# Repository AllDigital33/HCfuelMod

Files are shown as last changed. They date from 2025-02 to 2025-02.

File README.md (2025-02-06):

# HalfCat Mojave Sphinx Fuel Bulkhead Mod

OVERVIEW AND BACKGROUND

The HC Mojave Sphinx works great exactly as designed in HCR-5100. It is battle tested with over 50 firings and flights. 

After building, firing, and flying our Sinnoh Sphinx+ we noticed a small amount of IPA leaking from our fuel bulkhead when we went horizontal after filling and we noticed some small fuel leaks while pressurizing on the pad from camera footage post-flight. These leaks were minor and did not prevent the rocket from properly pressurizing, firing, or launching. The stock 4” aluminum tank tube and the +/- .013” ID tolerance is a wide variable, so we wanted to design a one-piece bulkhead with two o-rings to minimize the risk of a leak. 

We also were not fond of the two recovery bulkhead posts and their gasket washers, so we redesigned the aft recovery anchor plate to not use the bolts. That freed up room in the fuel bulkhead, so we added a 1/8” NPT tube and small valve we could use to fill fuel after the bulkhead had been secured to the tank. This allows us to assemble the piston and fuel bulkhead at home and then “load and go” on the range. 

SPECIAL CONSIDERATIONS

This mod, as designed, will only work if you are using a standard 4” fiberglass airframe for your recovery section. That was an upgrade in our original build. The stock Mojave Sphinx uses a cardboard recovery airframe that cannot support the snap forces of the drogue with the relocated aft recovery bulkhead (anchor).   

Read the attached PDF for more details.

Mike & Preston

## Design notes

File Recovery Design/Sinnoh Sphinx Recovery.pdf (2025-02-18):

# HalfCat Mojave Sphinx Sinnoh Sphinx+ Recovery

February 2025

# Modified Fiberglass Recovery

A big part of the "plus" in our Sphinx+ is the upgraded recovery section. It is a similar dual-deploy layout, but we used standard rocketry 4" fiberglass airframe and coupler, along with a commercial fiberglass nosecone (26" 5:1 Ogive). Our avionics bay is extended (13"), because we run our own flight computer ("Rocket Talk") and use a 12" 433 Mhz dipole antenna. Our avBay, nose, and aft bulkheads are all 1/8" aluminum with stainless steel u-bolt anchors. We use a nine foot Rocketman parachute and a three foot drogue with 1/2 kevlar shock cord from OneBadHawk. This gives us a soft landing in the 25fps range. Overall, our longer and heavier recovery section adds about five pounds to the build, but it is substantially stronger and will last longer (or survive harder landings).

The ID of 4" rocket fiberglass (e.g. Wildman Rocketry) is smaller than the cardboard ID specified in the Mojave Sphinx build, so you need to decrease the size of the INRG 200S airframe coupler to 3.9". The same is true for the Bulkhead Fuel Rec, AvBay bulkheads, and you will need a different bulkhead for the nose. In the nosecone we put our bulkhead about 6" from the tip and use the inside of the nose for the main chute.

Mike & Preston

@RocketTalk33 on the HC Discord

# Recovery Comparison

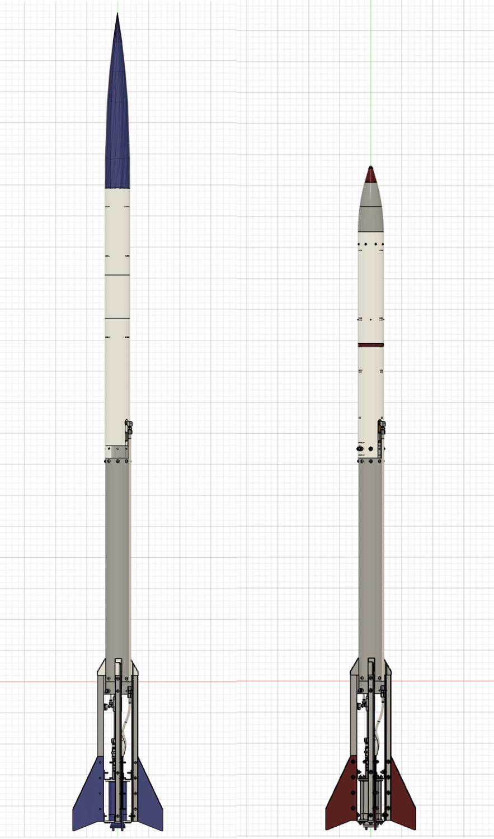
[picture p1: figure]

Sinnoh Sphinx+
(Fiberglass Recovery)

Mojave Sphinx

# Recovery Specs

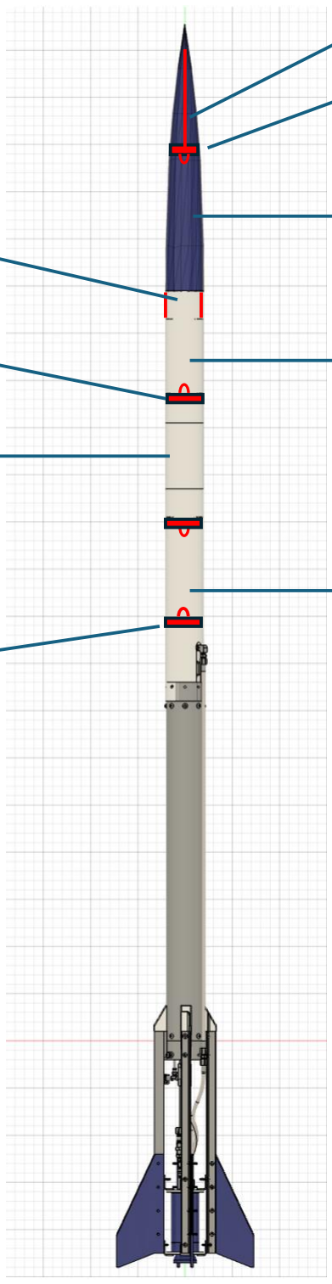
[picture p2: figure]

Sinnoh Sphinx+
(Fiberglass Recovery)

Lower (drogue) airframe
22.5” x 4” fiberglass
(can likely be a few inches shorter)

Upper (main) airframe
14” x 4” fiberglass

24” nosecone (5:1 ogive)
w/standard coupler

Internal bulkhead w/U-bolt (custom machined – see step)

Threaded Rod

Extended avionics bay for additional electronics
(regular build could use a 9” avBay coupler with 1.5” switchband)

Aluminum custom avBay bulkhead with U-bolt (avBay top and bottom)

Aluminum custom ”floating” bulkhead with U-bolt (details next page)

4-40 nylon shear pins (x4)

# Floating AFT anchor plate

3” coupler epoxied into airframe and reinforced with two PEM screws

Aluminum custom ”floating” bulkhead with U-bolt

5” floating coupler provides aft retention for the bulkhead.

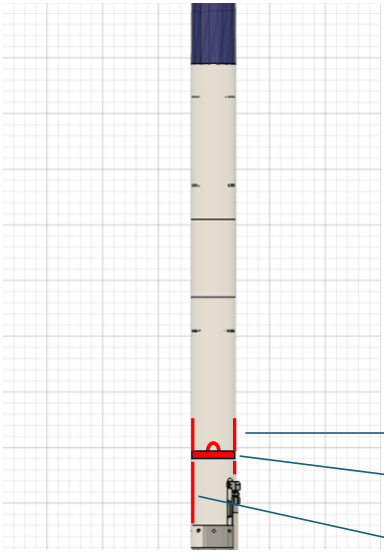
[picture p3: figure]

Note: use the same templates for airframe bolt holes and fuel plumbing cut-out. Use Dremel with carbon saw to cut fiberglass.

# Extended Avionics Bay

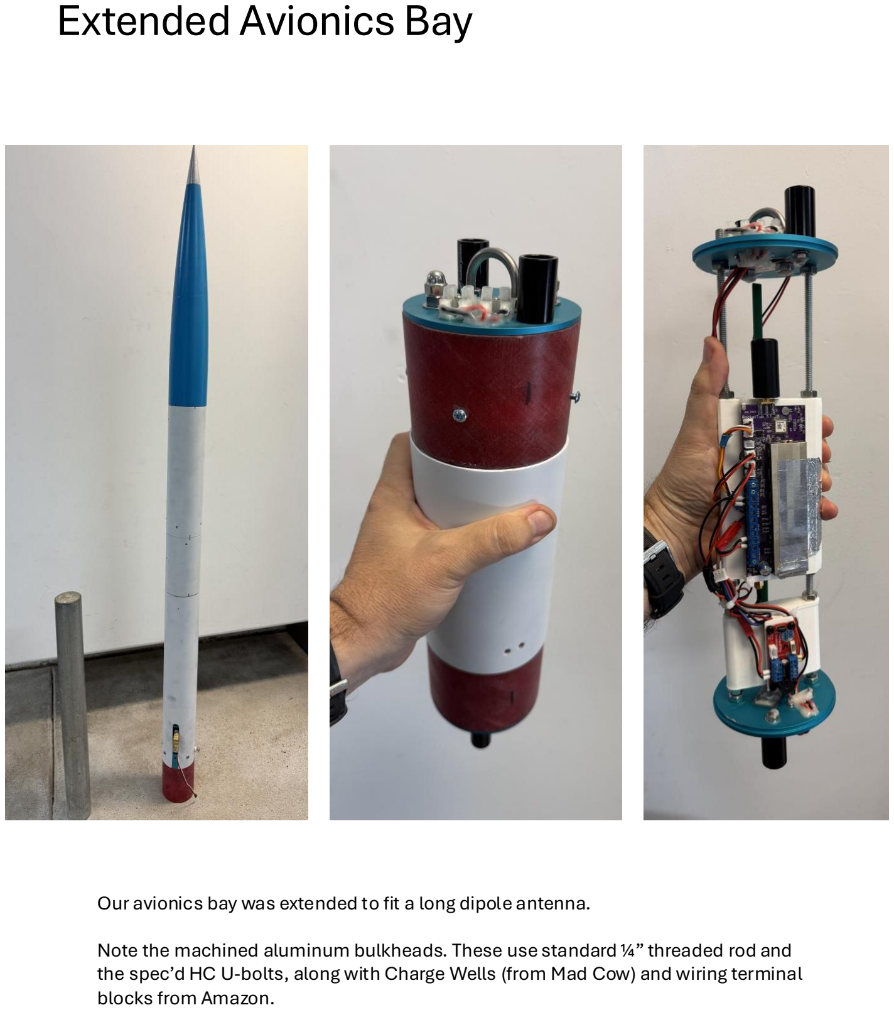
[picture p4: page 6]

Our avionics bay was extended to fit a long dipole antenna.

Note the machined aluminum bulkheads. These use standard ¼” threaded rod and the spec’d HC U-bolts, along with Charge Wells (from Mad Cow) and wiring terminal blocks from Amazon.

# BOM / Sources

Here is a list of the non-standard stuff we used for our recovery

1. 4” Fiberglass airframe (Wildman Rocketry link) (https://wildmanrocketry.com/collections/fiberglass-1/products/g12-4-0)
- Cut to 22.5” lower airframe and 14” upper airframe
2. 4” Fiberglass coupler for avBay (Wildman Rocketry link) (https://wildmanrocketry.com/collections/coupler-fiberglass/products/g12ct-4-0)
- Standard avBay would use 9”
3. 1” switchband for avBay (Wildman Rocketry link) (https://wildmanrocketry.com/collections/switch-band/products/switch-band-98mm-1-inch-wide)
4. 4” x 24” nosecone w/coupler 5:1 Ogive (Wildman Rocketry link) (https://wildmanrocketry.com/collections/nosecone/products/fnc4-0-5-1-vk-fw-mt-copy?variant=46732332695802)
5. Rocketman 9 foot standard chute (link) (https://the-rocketman.com/chutes.html/)
6. Rocketman 3 foot drogue (link) (https://the-rocketman.com/pro-x/)
7. 3/8” 30’ tubular Kevlar shock cord 3 loop (x2) (Mad Cow link) (https://www.madcowrocketry.com/3-8-x-30ft-tubular-kevlar-harness-with-3-sewn-loops/)
8. Nylon 4-40 shear pins x 4 (Chris’ rocket supplies link) (https://www.csrocketry.com/recovery-supplies/shear-pins/shear-pin-4/40.html)
9. Nosecone machined bulkhead (see STEP file)
10. avBay machined bulkhead x 2 (see STEP file)
1. Charge wells x 4 (link) (https://www.madcowrocketry.com/3-gram-aluminum-charge-wells/)
2. Terminal blocks (link) (https://a.co/d/2t4Hk0z)

For the lower airframe “floating” bulkhead see the other mod write-up here: https://github.com/AllDigital33/HCfuelMod/

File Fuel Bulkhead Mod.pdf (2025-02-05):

# HalfCat Mojave Sphinx Fuel Bulkhead Mod

Sinnoh Sphinx+ (SN05)
Feb 1, 2025

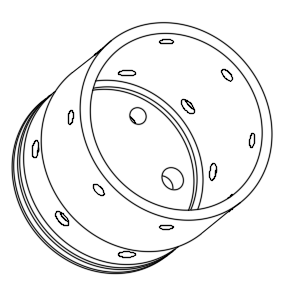
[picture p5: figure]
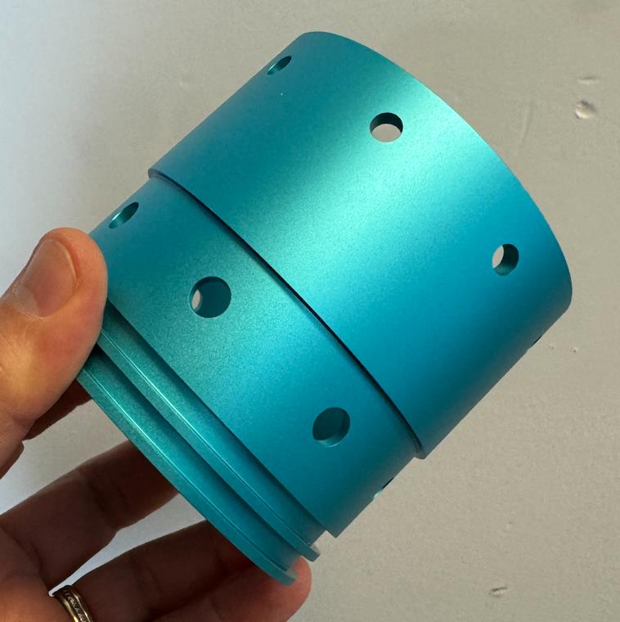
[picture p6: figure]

# Overview and Background

The HC Mojave Sphinx works great exactly as designed in HCR-5100. It is battle tested with over 50 firings and flights.

After building, firing, and flying our Sinnoh Sphinx+ we noticed a small amount of IPA leaking from our fuel bulkhead when we went horizontal after filling and we noticed some small fuel leaks while pressurizing on the pad from camera footage post-flight. These leaks were minor and did not prevent the rocket from properly pressurizing, firing, or launching. The stock 4” aluminum tank tube and the +/- .013” ID tolerance is a wide variable, so we wanted to design a one-piece bulkhead with two o-rings to minimize the risk of a leak.

We also were not fond of the two recovery bulkhead posts and their gasket washers, so we redesigned the aft recovery anchor plate to not use the bolts. That freed up room in the fuel bulkhead, so we added a 1/8” NPT tube and small valve we could use to fill fuel after the bulkhead had been secured to the tank. This allows us to assemble the piston and fuel bulkhead at home and then “load and go” on the range.

### Special Considerations

This mod, as designed, will only work if you are using a standard 4” fiberglass airframe for your recovery section. That was an upgrade in our original build. The stock Mojave Sphinx uses a cardboard recovery airframe that cannot support the snap forces of the drogue with the relocated aft recovery bulkhead (anchor).

Mike & Preston

@RocketTalk33 on the HC Discord

# Recovery Considerations

Our MS is using standard 4” rocketry fiberglass for the recovery airframe, along with standard 4” fiberglass coupler for the AvBay and a fiberglass nose cone. Ours is slightly oversized to provide for a larger avBay (flight computers) and larger parachutes.

This mod design and the step files assume standard composite airframes, which can be acquired from many vendors online (e.g., Wildman Rocketry or Mad Cow).


Sinnoh Sphinx+
(Fiberglass Recovery)

Mojave Sphinx

# Component Photos

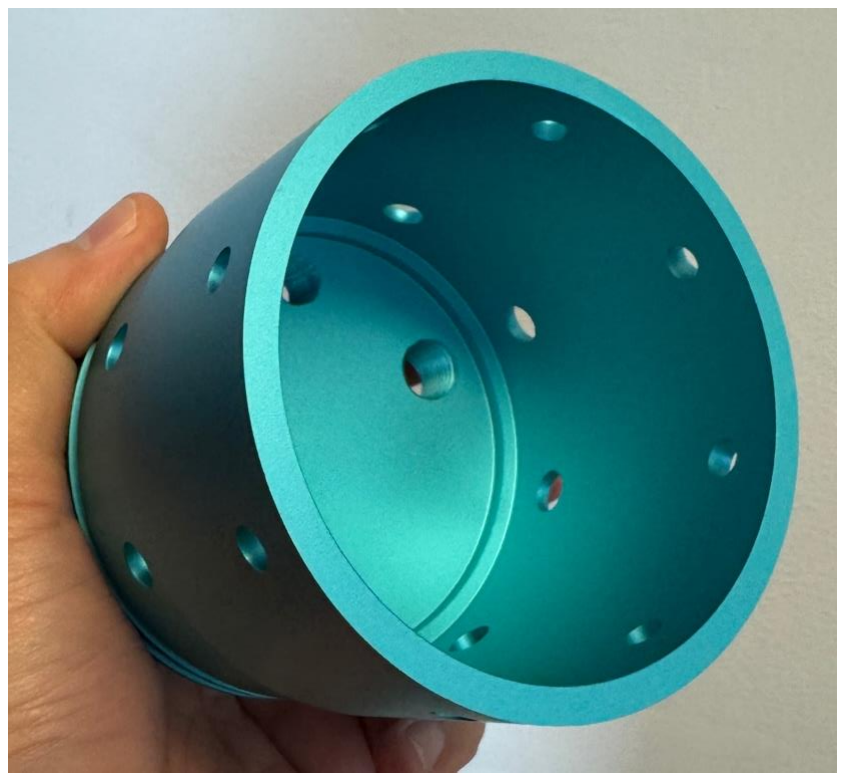
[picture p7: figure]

This is our new single piece double o-ring fuel bulkhead. It is much more stable than the two piece, but it requires a large solid round and a lot of machining to cut it down (or $76 to the kids in China). It is also slightly longer than the single o-ring design.

This is our new recovery bulkhead. It “floats” between two pieces of fiberglass coupler, inside the recovery airframe, so it is notched out on top and bottom. The forward piece of couple is epoxied into the airframe (along with two 5mm PEM nuts) providing forward retention and a floating piece of coupler is used aft of the bulkhead to provide reverse retention (pyro stops). This puts all the recovery snap forces onto the lower section of the fiberglass airframe, which is bolted into the tank.

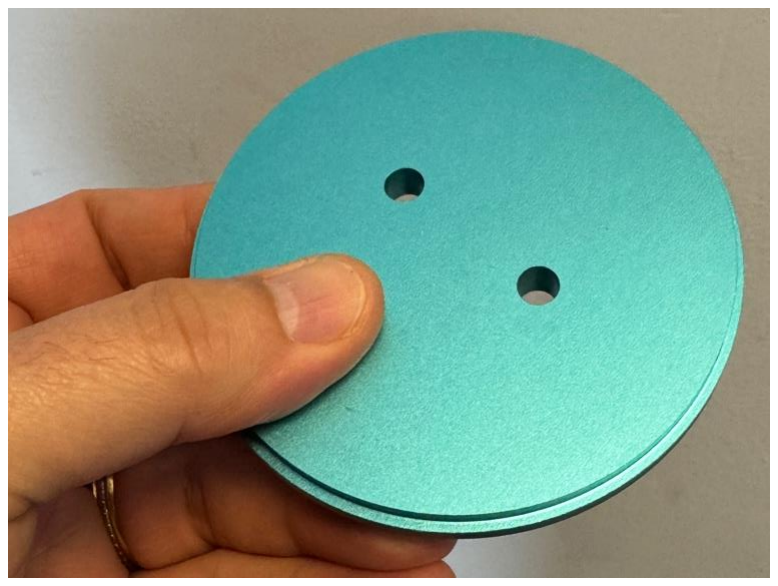
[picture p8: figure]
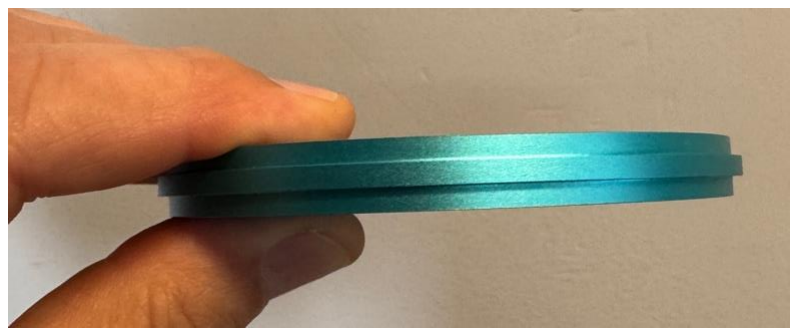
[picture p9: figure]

# Assembly Photos

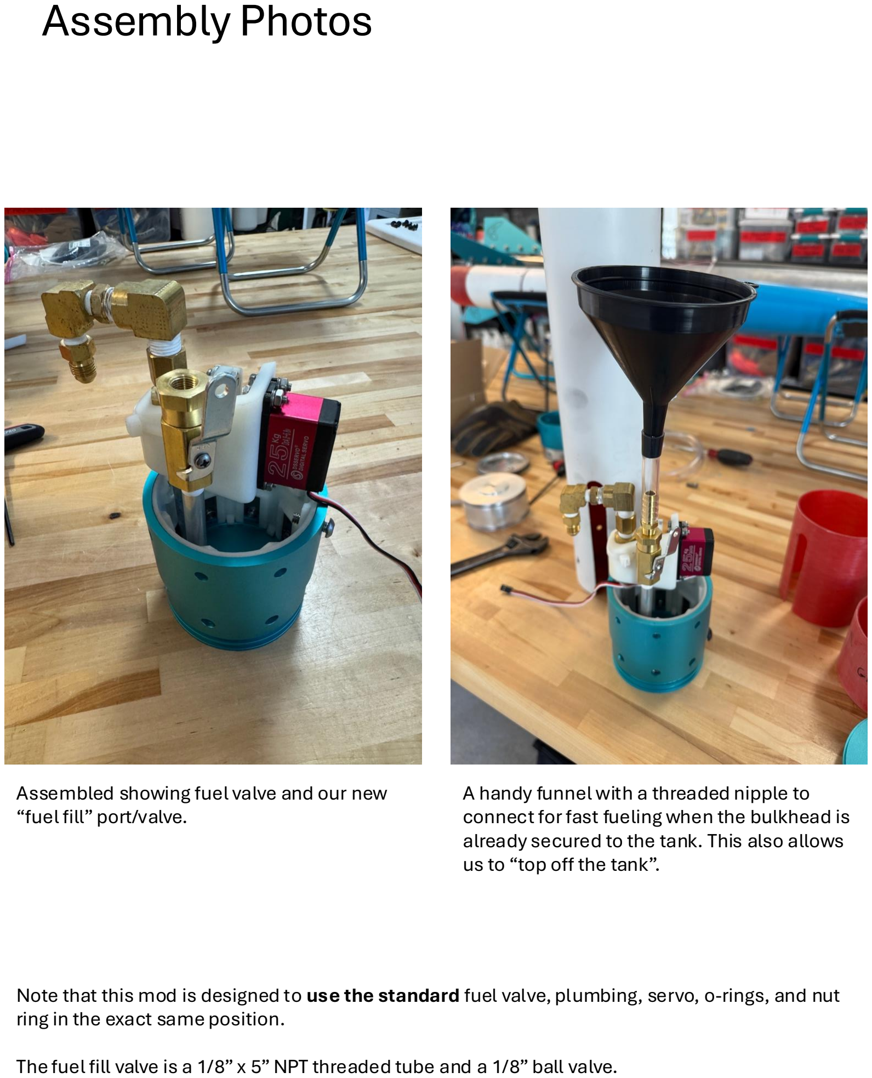
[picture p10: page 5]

Assembled showing fuel valve and our new “fuel fill” port/valve.

A handy funnel with a threaded nipple to connect for fast fueling when the bulkhead is already secured to the tank. This also allows us to “top off the tank”.

Note that this mod is designed to use the standard fuel valve, plumbing, servo, o-rings, and nut ring in the exact same position.

The fuel fill valve is a 1/8” x 5” NPT threaded tube and a 1/8” ball valve.

# Assembly Photos

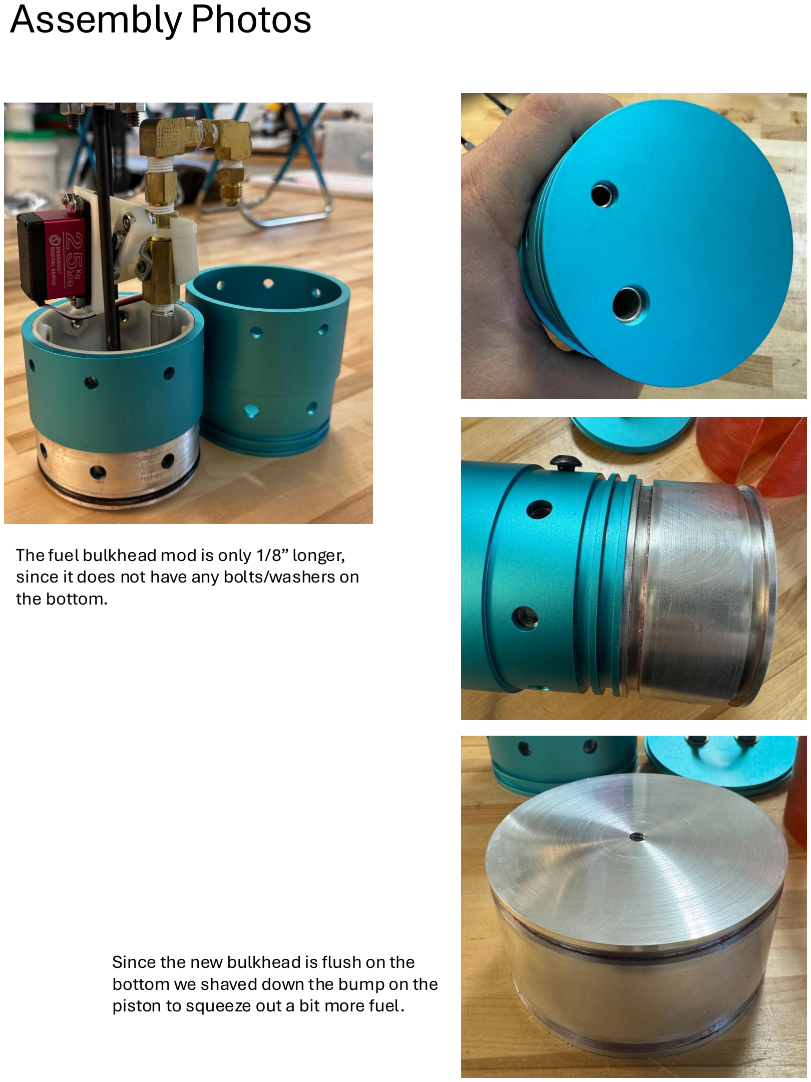
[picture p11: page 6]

The fuel bulkhead mod is only 1/8” longer, since it does not have any bolts/washers on the bottom.

Since the new bulkhead is flush on the bottom we shaved down the bump on the piston to squeeze out a bit more fuel.

# Assembly Photos

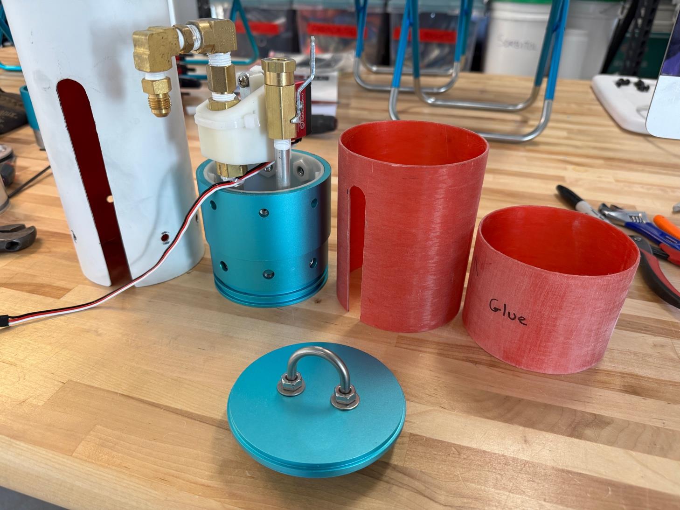
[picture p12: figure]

The four components of this mod include:

1. The new fuel bulkhead (machined)
2. The new recovery bulkhead (machined)
3. The forward fiberglass coupler stop (3” long - epoxied/screwed into the recovery airframe)
4. The aft fiberglass coupler stop (5” long – floating)

# Assembly Photos

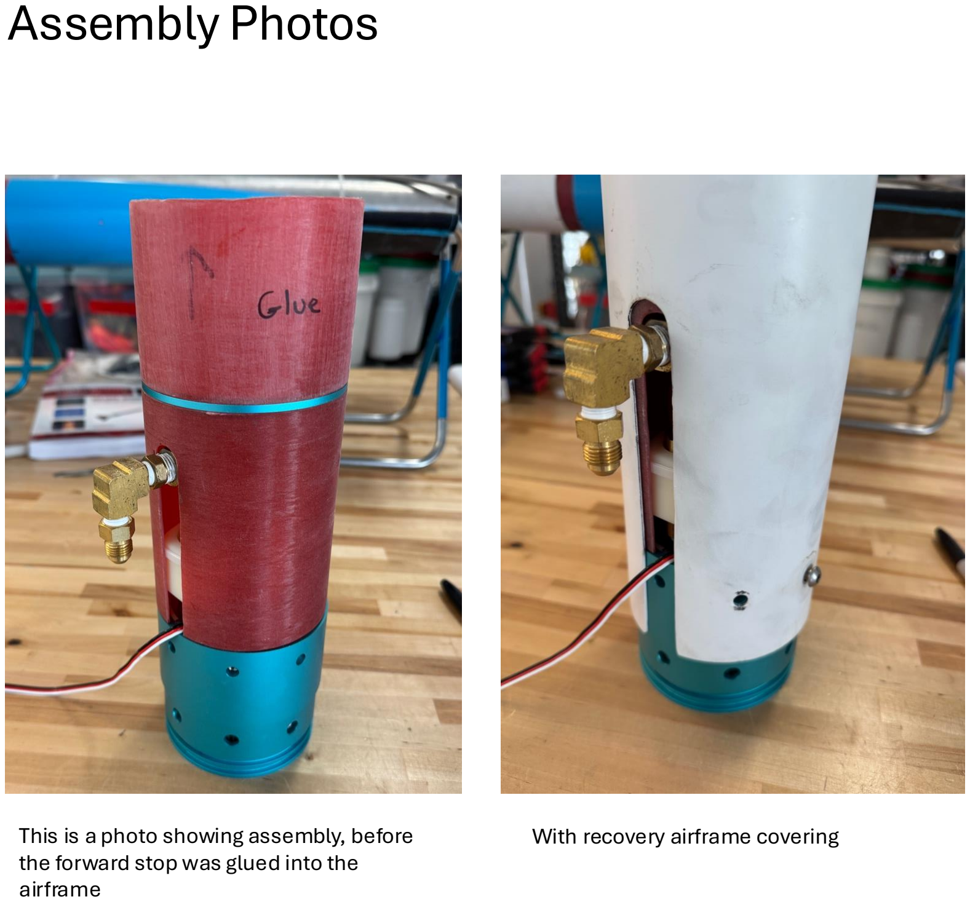
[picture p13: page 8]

This is a photo showing assembly, before the forward stop was glued into the airframe

With recovery airframe covering

# Assembly Photos

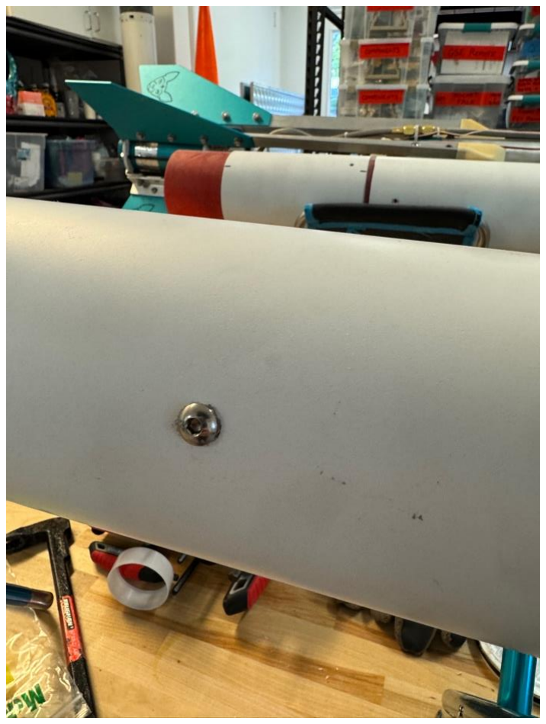
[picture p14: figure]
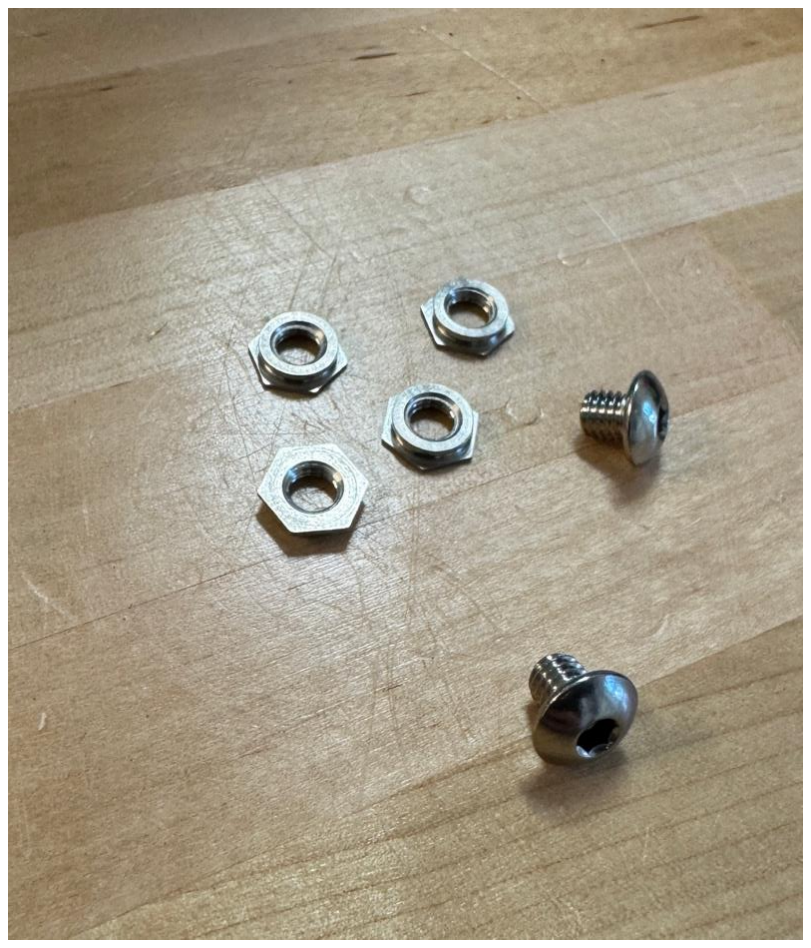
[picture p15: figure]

The 3” long piece of 4” fiberglass coupler is epoxied into the recovery airframe, such that the recovery bulkhead (anchor) sits tight with the aft coupler inserted and the airframe bolted to the tank. After the epoxy had dried we added two 5mm x 5mm bolts using four PEM nuts. This is a form of retention we have used on very large solid motor rockets. You likely could just use four nuts with PEM screws or just epoxy, but we double up (“belts and suspenders”) when it comes to recovery.

To properly epoxy the coupler inside, do the following: 1) sand the ID of the airframe and the OD of the coupler 2) clean the surfaces well with IPA 3) use a high quality epoxy with a long cure time (we use Loctite Hysol EA E-20HP) 4) coat the inside of the airframe well around 8-10” from the aft end using your hands and a rubber glove 5) assemble the aft coupler stop, the recovery bulkhead and the forward coupler together on the tank (fuel bulkhead) 6) slide the airframe over and bolt onto the fuel bulkhead, such that the forward coupler is now in perfect position 7) let dry in a horizontal position, so epoxy doesn’t drip down onto the recovery bulkhead.

# BOM

Here is a list of the non-standard stuff we used for this mod…

1. Machined fuel bulkhead (step file here) (https://github.com/AllDigital33/HCfuelMod)
2. Machined recovery bulkhead (step file here) (https://github.com/AllDigital33/HCfuelMod)
3. 4” standard rocketry fiberglass coupler (5” length & 3” length) (Wildman) (https://wildmanrocketry.com/collections/coupler-fiberglass/products/g12ct-4-0)
4. Fuel fill valve
1. 1/8” NPT x 5” aluminum pipe (44665K308)
2. ¼” NPT ball valve (McMaster 4112T12)
5. Epoxy – Loctite EA E-20HP
6. PEM nuts
1. 5mm x 5mm hex screws (McMaster 92095A308)
2. 5mm PEM nuts (McMaster 94674A606)

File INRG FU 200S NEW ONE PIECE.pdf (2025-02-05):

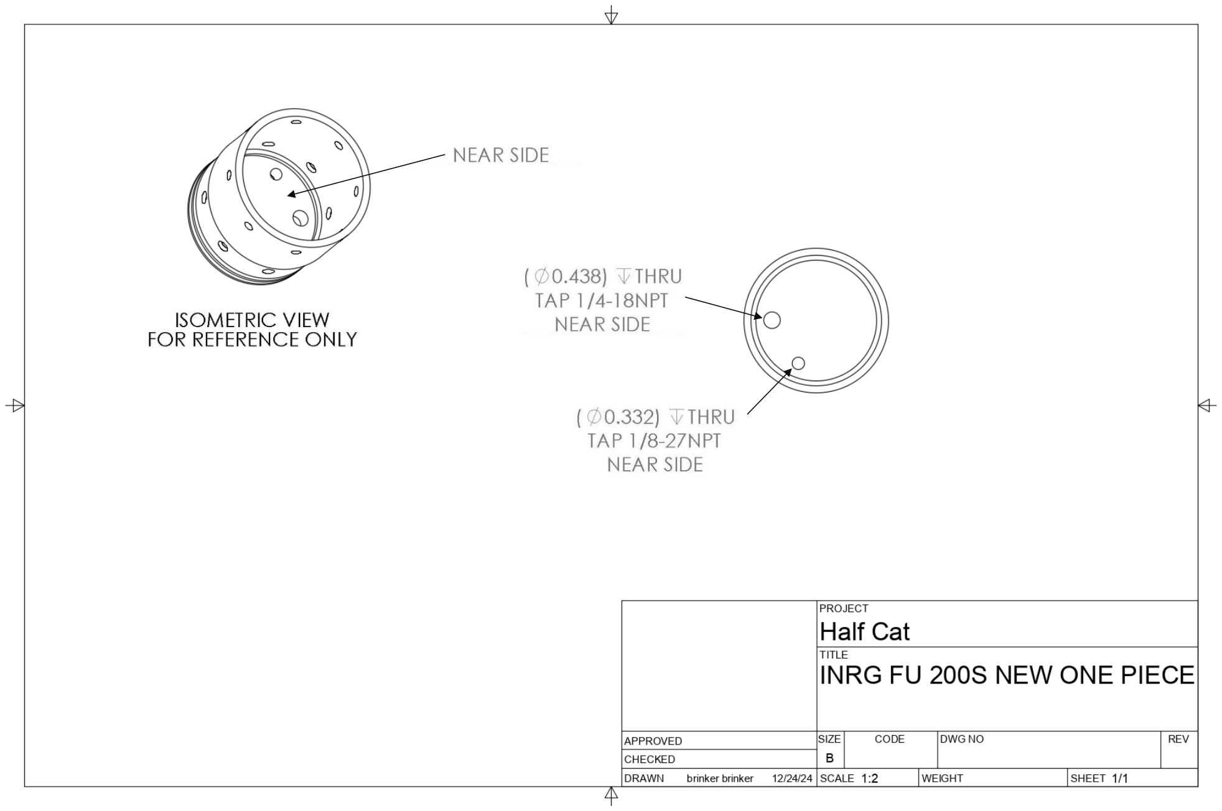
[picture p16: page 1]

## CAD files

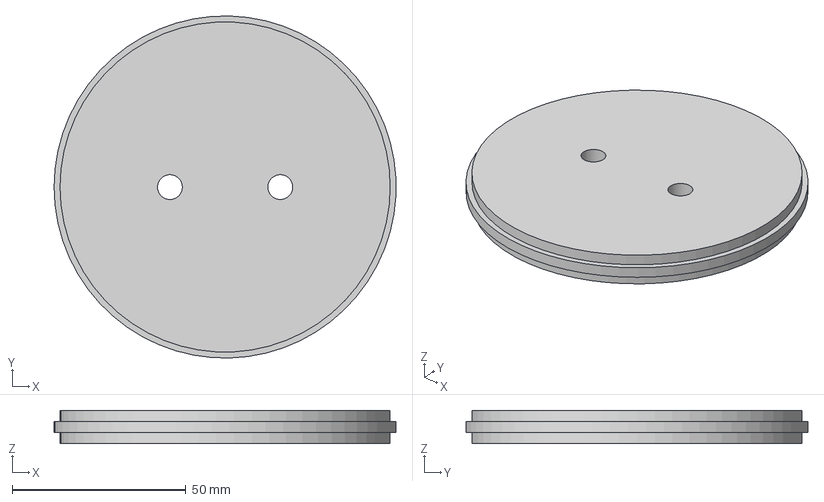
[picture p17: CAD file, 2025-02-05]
BKHD-REC-LOWER.step
98.4 x 98.4 x 9.52 mm

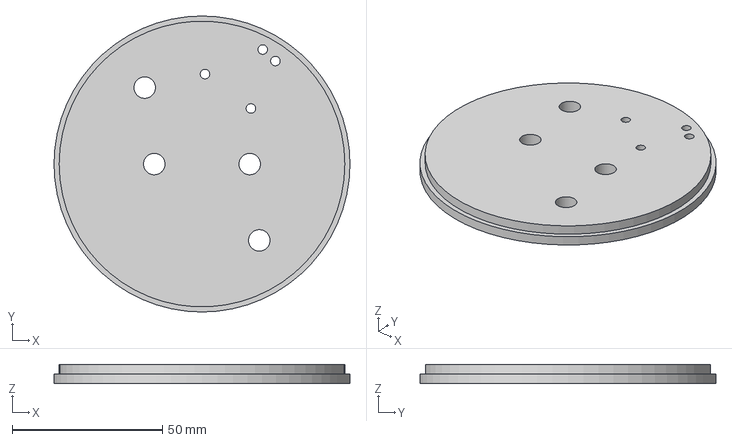
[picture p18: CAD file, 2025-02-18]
Recovery Design/BKHD AVBAY REC 4X250C 2X170WE.step
98.4 x 98.4 x 6.35 mm

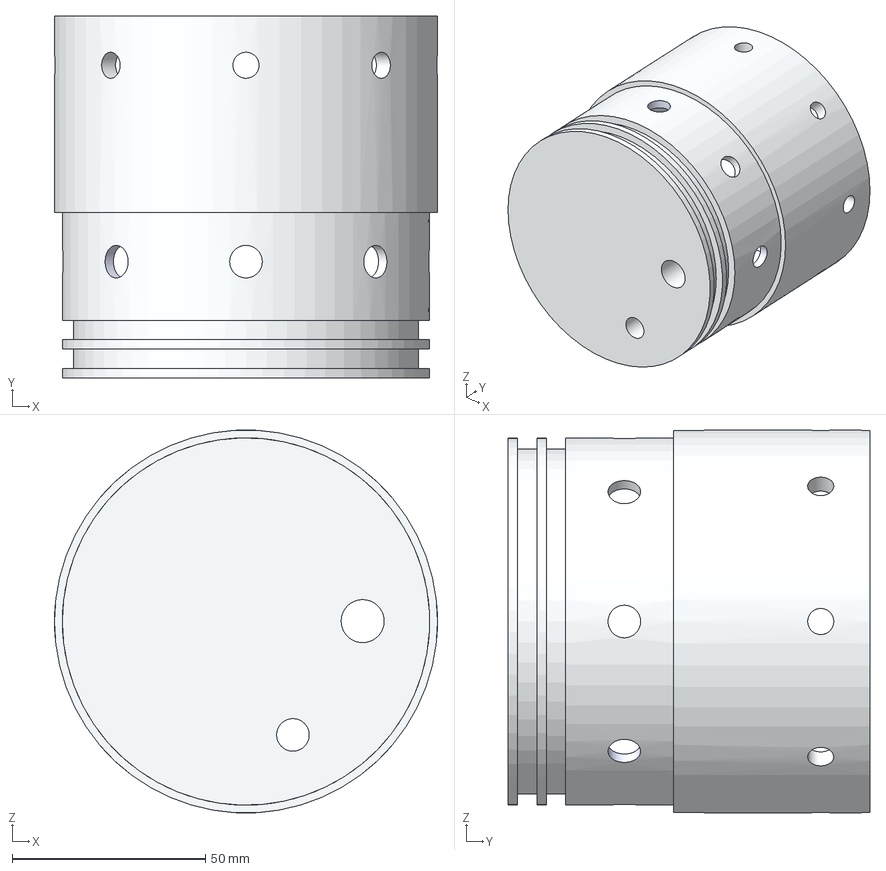
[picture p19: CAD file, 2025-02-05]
INRG FU 200S NEW ONE PIECE.step
99.1 x 93.5 x 99.1 mm

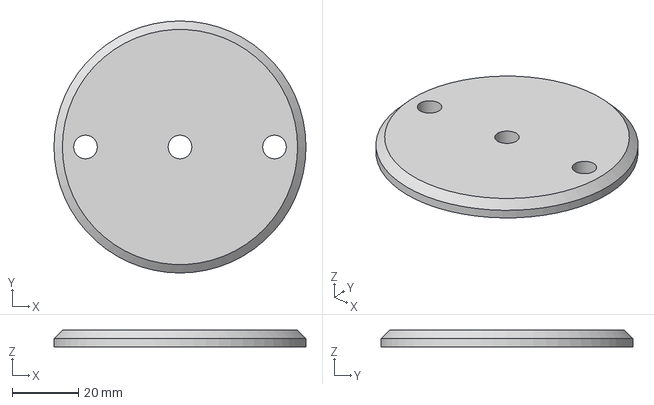
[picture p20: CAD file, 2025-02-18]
Recovery Design/BLKHD NOSE SMALL.step
76.2 x 76.2 x 5.08 mm

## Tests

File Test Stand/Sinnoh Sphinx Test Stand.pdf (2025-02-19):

# HalfCat Mojave Sphinx Sinnoh Sphinx+ Test Stand

February 2025

# Test Stand Overview

We have been testing long 4” (98mm) motors out at FAR using the same basic test stand design for 8+ years, so for our Mojave Sphinx we just made small modifications. We’ve had some huge APCP motors cato without ”going dynamic” and leaving the stand like the Chinese Tianlong-3.

For our Mojave Sphinx version we’ll explain the design in two parts: 1) the test stand that bolts to the I-beam at FAR and 2) the “cat hat” topper we put on the rocket to protect the fuel bulkhead and secure it to the stand.

The Test Stand:

Our test stand (“rig”) is just three parts and the load cell:

- A 55” x 8” x .25” aluminum backplate
- A 6”x6” x .4” steel 90 degree bracket (ours is 10” wide but only needs to be 6” wide)
- A 4” dock slider used for lake dock poles (see BOM)
- A pancake style load cell providing an anchor point and positive/negative measurement

The Rocket:

On the rocket we used a stock 4.5” OD aluminum tube with a cut-out that slides over the fuel bulkhead and bolts into the upper airframe nut ring. Then we have a custom machined “hat” that bolts into the aluminum tube and is secured into the load cell with a 16Mx1.5 threaded bolt. The hat also bolts into the aluminum tube for negative (gravity) retention. So, we just have the following two parts:

- A 4.5” OD / 4.0” ID x 12” long aluminum tube with cut-outs for the fuel line and indexed holes
- A custom machined “hat” with a 16M threaded hole and indexed holes for retention

The rig bolts to the FAR large I-beams using ½” bolts (2”+ long) with a 4” x 4” x 4” pattern. We use 4 bolts on the aluminum back plate and 4 bolts on the steel angle stop.

Mike & Preston
@RocketTalk33 on the HC Discord

# On the I-Beam

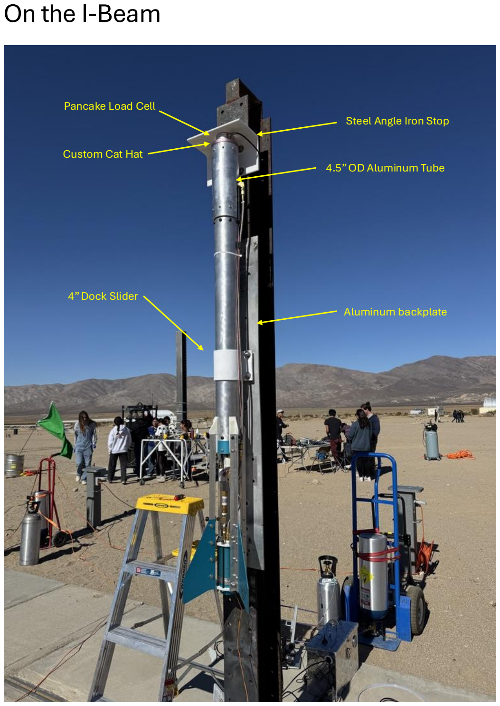
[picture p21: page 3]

4” Dock Slider
Aluminum backplate

Steel Angle Iron Stop

4.5” OD Aluminum Tube

Pancake Load Cell

Custom Cat Hat

# Dock Slider

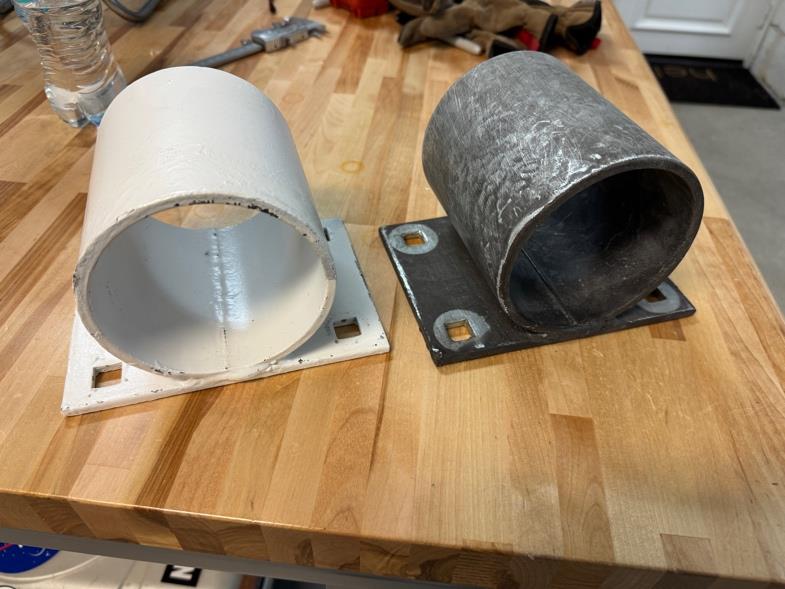
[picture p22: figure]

4” Dock Slider from DockHardware.com (part number DH PH-HO4 ).

The left one is cleaned up with the inside weld seam sanded down and painted. On the right is old one in our shop that has seen a few cato’s. These things are tough!

We fasten these to the aluminum backplate using ½” bolts with the heads on the back of the plate and threads sticking up and we use one nut as a spacer (see photo below) to align to the stand-off height of the Mojave Sphinx.

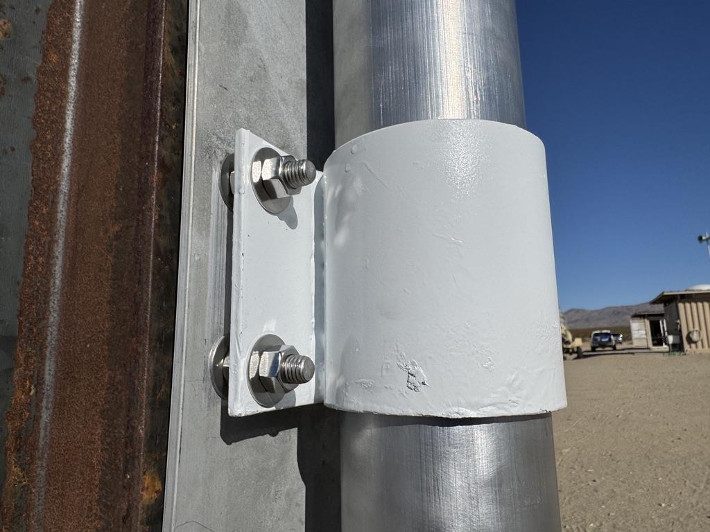
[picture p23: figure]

# Steel Stop

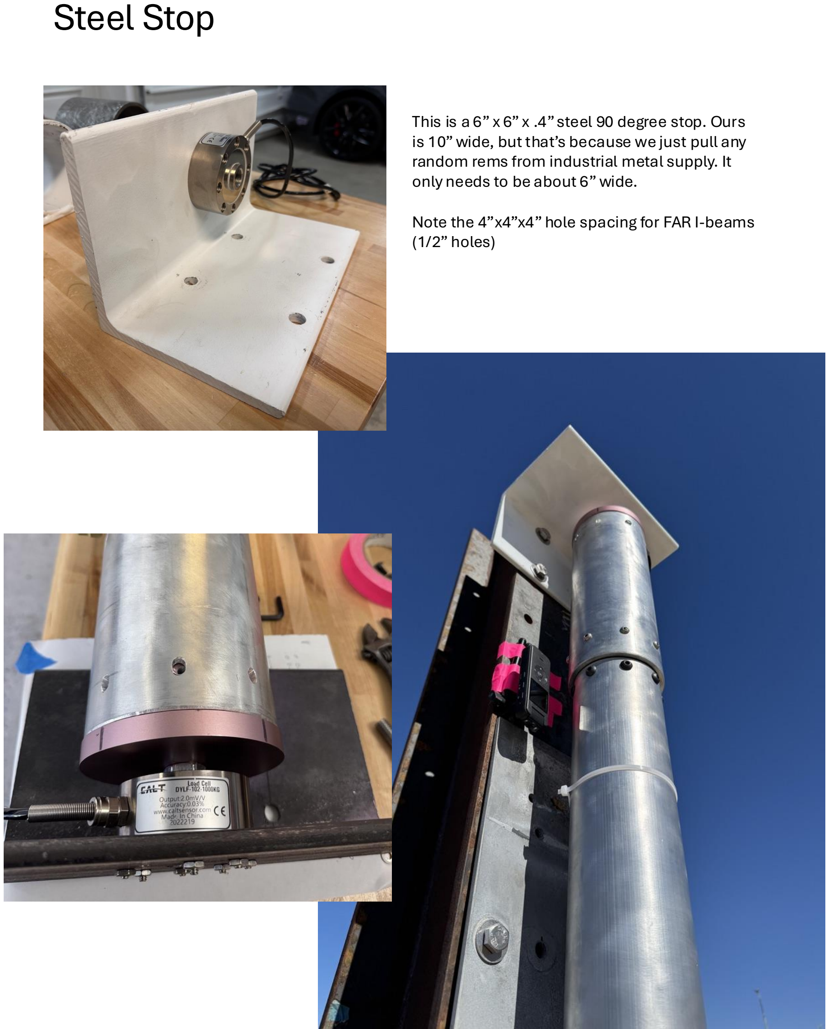
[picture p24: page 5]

This is a 6” x 6” x .4” steel 90 degree stop. Ours is 10” wide, but that’s because we just pull any random rems from industrial metal supply. It only needs to be about 6” wide.

Note the 4”x4”x4” hole spacing for FAR I-beams (1/2” holes)

# The ”Cat Hat”

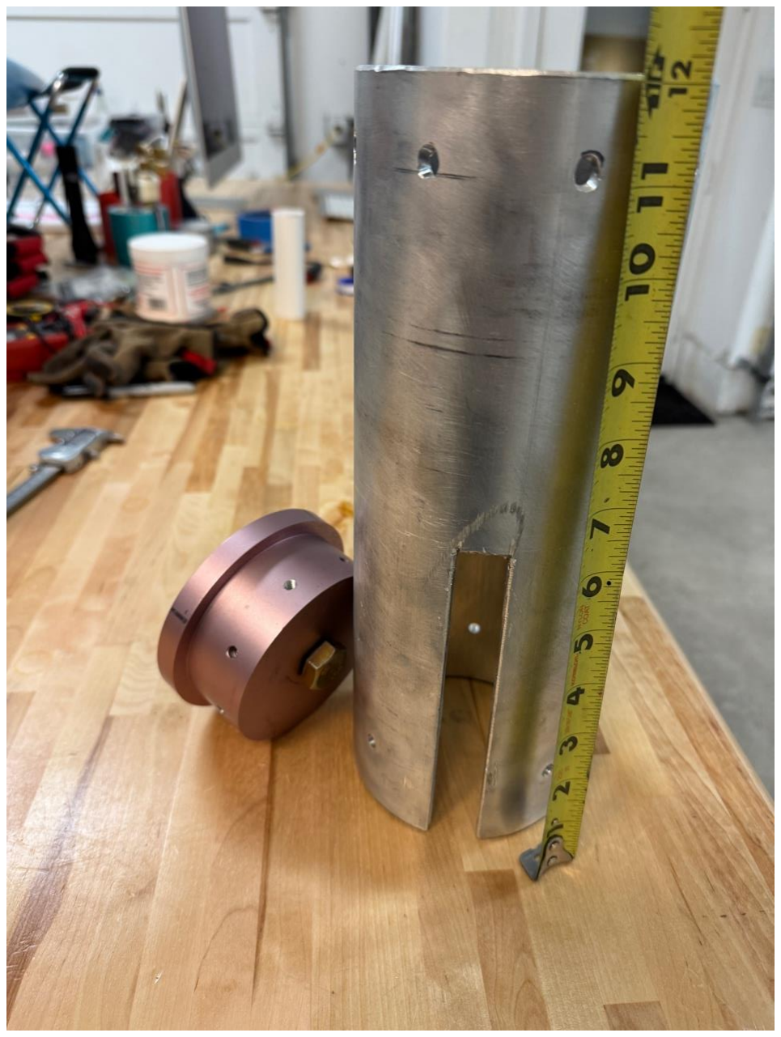
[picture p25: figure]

Our “Cat Hat” is two pieces designed to slip over the top of the fuel bulkhead assembly and the recovery bulkhead in the standard MS design. It is bulky and heavy, but worked well to distribute the weight and is easy and fast to assemble on-site.

The tube is stock aluminum 4.5” OD / 4.0” ID x 12” from McMaster Carr. We hacked out the slot for the fuel line using a 4” grinder with a carbon blade and index drilled the holes using a 3D printed guide to match the Mojave Sphinx upper airframe nut ring pattern.

The pink “hat” in the photo was a quick CAD hack sent out for machining. This version is embarrassingly oversized and feels like a brick, but it does the job. It has a M16 threaded hole down the center to match our pancake load cell center-threads and is indexed with ¼”-20 threaded holes around the outside. It only needs 2-3 bolts at the top to hold the weight of the rocket before firing.

# The ”Cat Hat”

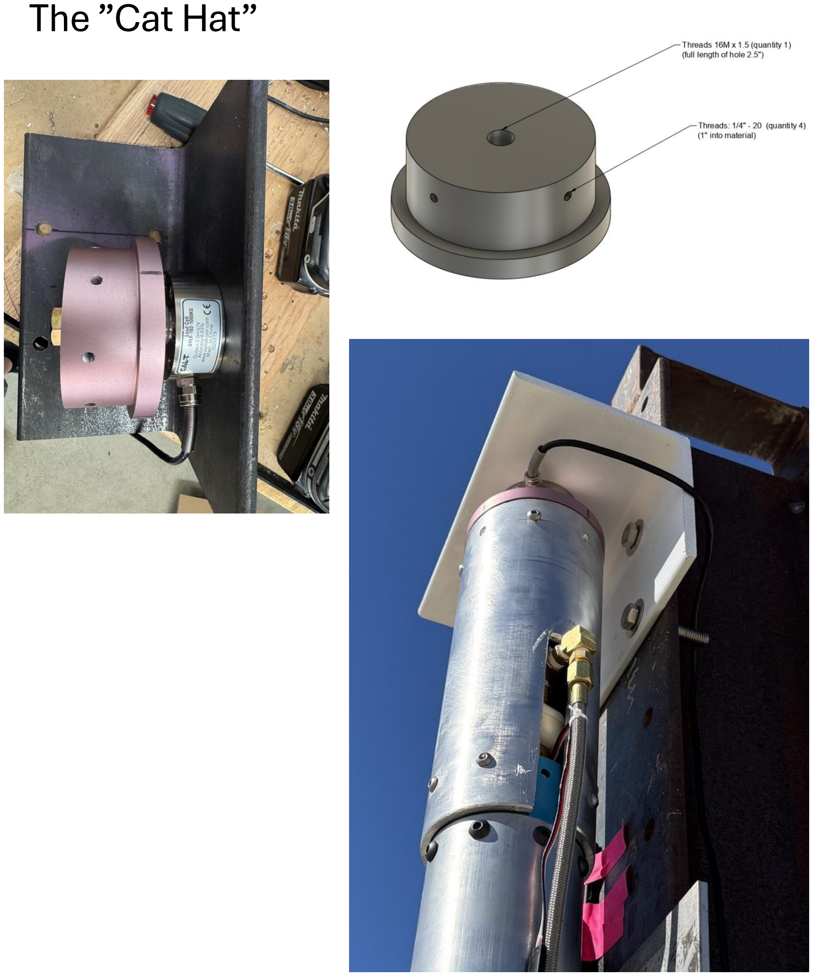
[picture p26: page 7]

# Order of Operation

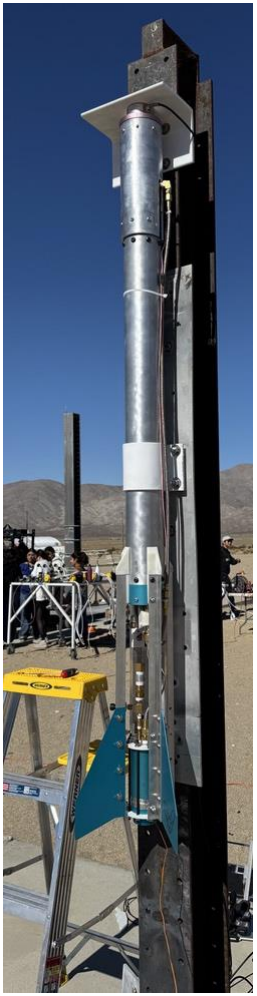
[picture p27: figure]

Here is our order of operation to make test set up smooth:

Before you get to the I-beam (or at home/school):

1. Insert dock slider bolts into the backplate and secure with the spacer nuts
2. Ensure the load cell is bolted to the angle stop

I-Beam initial setup:

1. Attach the angle stop four bolts
2. Screw in the ”cat hat” to the load cell (finger tight)
3. Attach the aluminum backplate with four bolts
4. Attach load cell to DAQ – test DAQ – prep GSE

Rocket setup:

1. Before filling fuel, with the fuel bulkhead off, slide the dock slider over the tank
2. Fill fuel and secure the fuel bulkhead then attach the 4.5” aluminum top tube using all seven lower bolts.

I-Beam rocket load (two people):

1. Secure the aluminum top tube to the cat hat using three bolts at the top
2. Align and secure the dock slider and secure with the four nuts
3. Secure the remaining connections for firing (N2O line, servo umbilical, etc.)

# BOM / Sources

Here is a list of the stuff we used for our test stand

1. Aluminum backplate 55” x 8” x .25” (Rem from industrial metal supply)
2. Steel 90 degree stop – 6” x 6” x 10” wide x .4” thick (Rem from IMS)
3. 4” Dock Slider from DockHardware.com part DH PH-HO4 (link here) (https://www.dockhardware.com/product/4-galvanized-pipe-holder-0n-5-x-6-75-backer-plate/)
4. Aluminum tube 4.5” OD / 4.0” ID x 12” long (McMaster-Carr 9056K32)
5. Custom machined “hat” insert
6. ½” x 2” fasteners x 12 - bolts, nuts, washers (with 4 extra nuts for spacing)
7. Pancake load cell (ours is 1000Kg, but smaller is fine for HC) Amazon link here (https://a.co/d/9E6gFYI)
